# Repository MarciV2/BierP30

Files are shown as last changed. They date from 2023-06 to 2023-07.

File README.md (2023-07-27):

# BierP30 / Weißer Hase / Keba P30 Bierzapfsäule

Servus Melissi und E-Bastian,
Ich hoffe, euch hat unser Geschenk gefallen!

Damit ihr's auch öfters verwenden könnt hier eine kleine Anleitung und ein paar Tipps.

## Funktionsweise
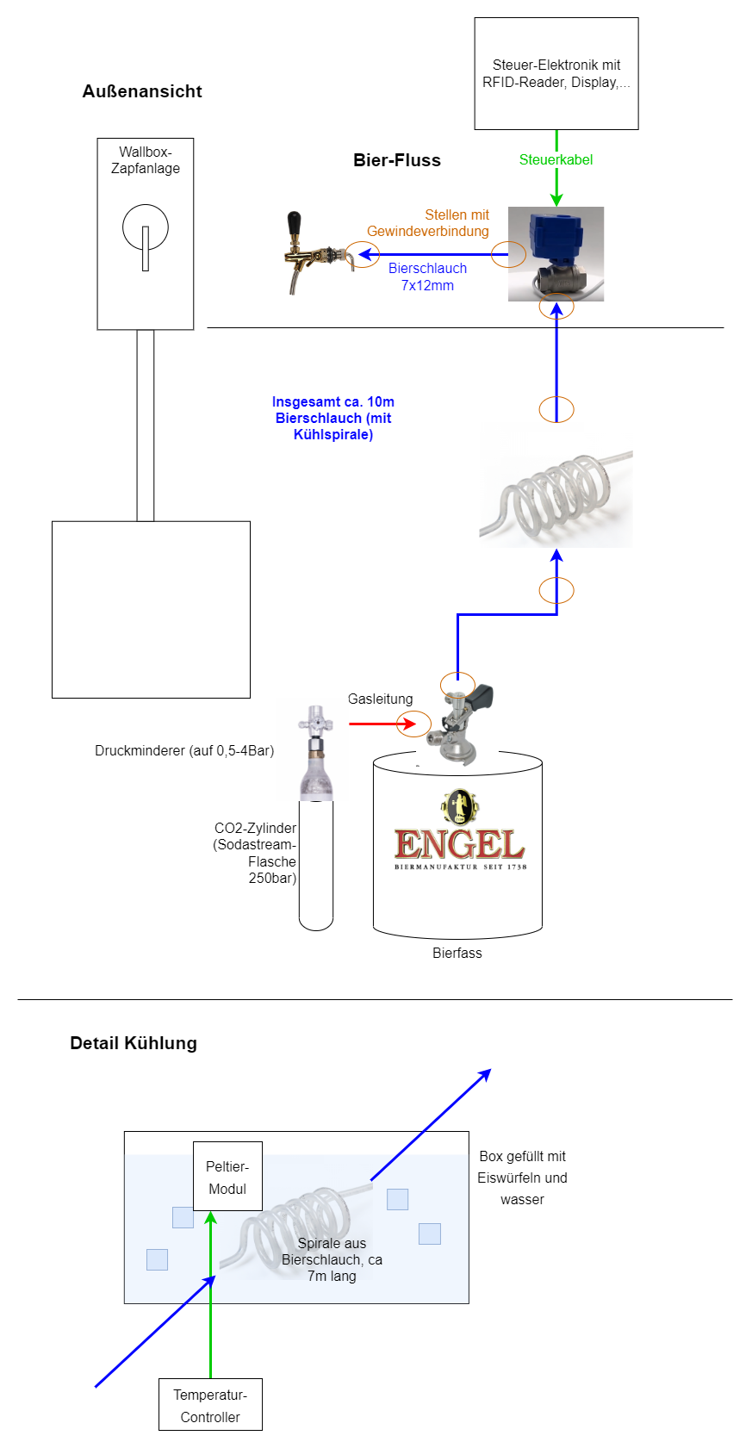
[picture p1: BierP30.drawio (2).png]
BierP30.drawio (2).png


Das Bier befindet sich anfangs im (idealerweise vorgekühlten) Fass, CO2 in der Sodastream-Flasche.
Prinzipiell wird das Gas (über einen Druckminderer) und den Fassanschluss (seitlicher Anschluss) in das Fass geleitet, wo es von oben auf das Bier drückt. Das Bier kann über ein Steigrohr im Fass durch den oberen Anschluss des Fassanschlusses und die Schläuche raus.
Das Bier fließt dann durch die Schlauchspule, welche sich in Eiswasser befindet, gekühlt in die Wallbox hoch. (den Kasten mit "Peltier-Modul" bitte ignorieren, das Feature mussten wir leider weglassen) Oben in der Wallbox ist ein Servo-getriebenes Kugelventil, das durch die Steuer-Elektronik geöffnet oder geschlossen werden kann. Beim Ausschalten der Anlage bleibt das Ventil im aktuellen Zustand. Dies ist relevant, wenn ihr nicht jedes Mal eine Karte vorhalten wollt oder zum Reinigen.
Vom Ventil fließt das Bier zum Zapfhahn. (Mehr dazu im Kapitel [Zapfen](##Zapfen))
Durch den Zapfhahn dann ins Glas und von dort dann endlich eure Rachen hinunter.

## Aufbauen
1. Bleck-Box in die Holz-Box stellen
2. etwa 6kg Eiswürfel in die Blech-Box füllen
3. (idealerweise kaltes) Wasser in die Blech-Box bis etwa 8cm unter dem Rand füllen
4. Deckel der Blech-Box mit der Kühlspirale aufsetze, sodass isolierter Schlauchabgang nahe an der Holzwand ist
5. 3-Poligen Stecker von Deckel der Blech-Box an Spelsberg-Gehäuse anschließen
6. (zuvor auf Minimum gedrehten) Druckminderer auf Sodastream-Flasche drehen (zischt mal kurz, einfach weiter drehen)
7. Sodastream-Flasche mit Spanngurt an Bierfass befestigen
8. Gasleitung von Druckminderer an seitlichen Anschluss des Fassanschlusses anschließen
9. weißes Plastikteil mit dem Keil nach oben (Rundung unten!!!) in den oberen Anschluss des Fassanschlusses legen (soll wohl helfen, dass es weniger schäumt)
10. Bierschlauch an oberen Anschluss des Fassanaschlusses anschließen und am anderen Ende an das nicht isolierte Schlauchstück der Kühlspirale. Schlauch in die vorgesehene Aussparung in Holz-Box legen. Zur Verbindung von Bierschläuchen werden die "Rohrstücke" mit den "Flügeln" verwendet.
11. Schaumstoff-Isolierung um Bleck-Box platzieren (evtl. mit Spanngurt sichern)
12. Deckel der Holz-Box (mit U-Profil und Wallbox) teilweise auf die Holz-Box setzen
13. Stecker von Wallbox an Spelsberg-Gehäuse anschließen
14. Bierschlauch von Wallbox an isolierten Abgang von Kühlspirale mittels "Rohrstück mit den Flügeln" anschließen
15. Holz-Deckel sauber auf Holz-Box aufsetzen (Deckel hat ebenfalls Aussparung für Bierschlauch)
16. Fassanschluss auf Fass schieben und Hebel nach unten drücken bis er einrastet.
17. Schuko-Stecker anschließen (wenn Kartenfunktion gewünscht oder Ventil noch geschlossen)
18. Druckminderer aufdrehen (Vollgas! (~2-2,5 Bar) Falls es pfeift -> minimal runterdrehen)

## Zapfen
1. Ladekarte vorhalten und erstmal 2-5l Schaum zapfen (da kommt am Anfang immer sehr viel!! nicht wundern)
2. Der seitliche Hebel am Zapfhahn steuert die Durchflussmenge. Idealerweise mit sehr wenig (oben) starten und beim Zapfen dann öffnen (nach vorne/unten), bis akzeptabel viel Schaum kommt.
3. Wenn der seitliche Hahn ohne übermäßigen Schaum aufgedreht werden kann, evtl den Druck am Druckminderer etwas geringer einstellen. Schaum ist eine Balance zwischen Temperatur, Druck und Durchfluss, wenn das Bier zu warm ist, schäumt es stärker, wenn der Durchfluss zu hoch ist ebenso. Bei zu wenig Schaum (wird vermutlich nicht vorkommen) könnte es zu viel Druck oder Reste vom Reinigen sein. Andere Biersorten schäumen ebenfalls sehr verschieden.
4. Für Cola, Sprudel,... ist ein deutlich höherer Druck als für Bier notwendig. Dazu bräuchtet ihr dann einen anderen Druckminderer (+ Gasflasche) aber wer will schon Sprudel, wenn man Bier haben kann?!?

Wenn bei warmem Wetter länger nichts gezapft wurde evtl. die ersten 100ml wegschütten, da diese im Schlauch zur Wallbox hoch schnell warm werden.

## Zerlegen

## Reinigen

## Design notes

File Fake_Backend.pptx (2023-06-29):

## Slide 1

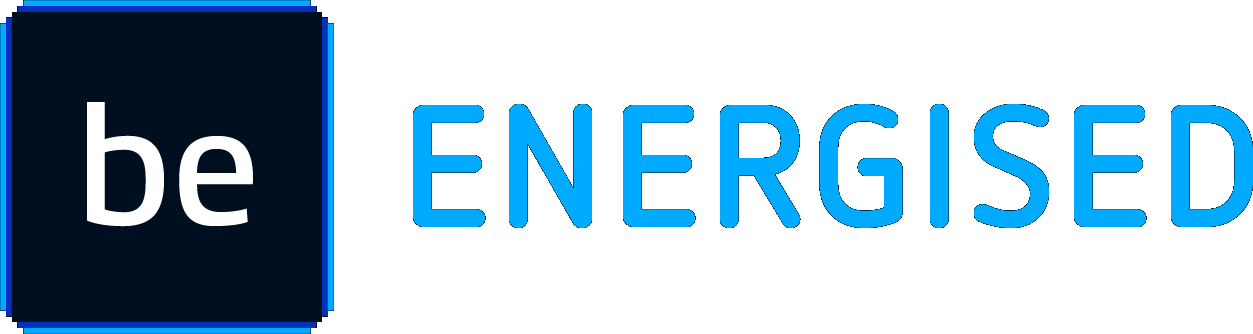
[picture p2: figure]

Dashboard

DB Hochzeit Sebastian & Melissa

Infrastruktur CRM Finanzen Aufgaben Einstellungen

>

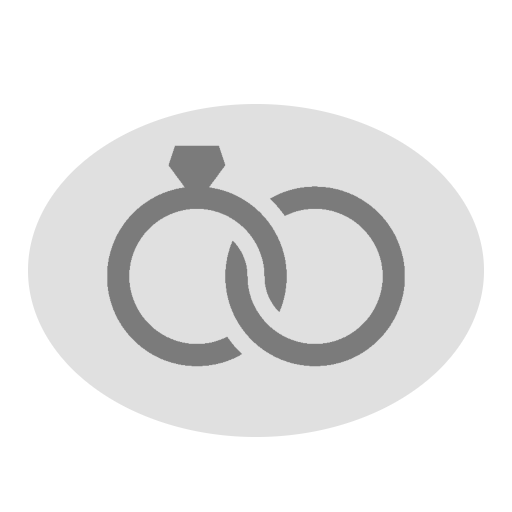
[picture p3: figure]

>

>

>

>

12

Jahre zusammen

1

Tage verheiratet

Tage verheiratet

1

Platzhalter Gruppenbild

Ganz viel Glück, Freude und Spaß wünschen euch die TSE-ler

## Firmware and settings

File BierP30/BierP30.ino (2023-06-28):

#include <SPI.h>
#include <Wire.h>


int BEER_VALVE_OPEN_TIME = 40;
#define BEER_VALVE_RELAIS_PIN 5

long beer_valve_open_millis = 0;
bool beer_active = false;

bool refill_ice = false;



void setup() {
  Serial.begin(9600);
  Serial.println("Starting...");
  SPI.begin();  // Init SPI bus
  Wire.begin(); 


  initLedMatrix();
  initLedStripe();
  initRFID();
  initTemp();

 
  pinMode(BEER_VALVE_RELAIS_PIN, OUTPUT);
  digitalWrite(BEER_VALVE_RELAIS_PIN, LOW);
}

void loop() {

  //Timer checks
  if (beer_active) {
    //Timer-Bar anpassen
    long beer_millis_elapsed = millis() - beer_valve_open_millis;
    uint8_t beer_timer_percent = 100 - round(beer_millis_elapsed / (BEER_VALVE_OPEN_TIME * 10));
    setBeerTimerBar(beer_timer_percent,255,170,0,false);

    //Zapfphase zu ende -> stoppen
    if (beer_timer_percent <= 0) {
      stopBier();
    }
  }

  displayTimerEvent();
  ledStripeTimerEvent();
  rfidTimerEvent();
  tempTimerEvent();
  
}



// Funktion wird aufgerufen, wenn Autentifizierung mit FreiBierKarte erfolgreich
void startBier() {
  beer_valve_open_millis = millis();
  digitalWrite(BEER_VALVE_RELAIS_PIN, HIGH);
  beer_active = true;
  if(refill_ice) displayMessage("Eis nachfuellen", false);
  else displayMessage("Ozapft is", false);
}


void abortBier(){
  setBeerTimerBar(100,255,0,0,true);
  digitalWrite(BEER_VALVE_RELAIS_PIN, LOW);
  beer_active = false;
}

// Funktion wird aufgerufen, wenn der Timer des Biers abgelaufen ist
void stopBier() {
  Serial.println("Timer abgelaufen, Prost!");
  digitalWrite(BEER_VALVE_RELAIS_PIN, LOW);
  beer_active = false;
  displayMessage("Prost", true);
  setBeerTimerBar(100,0,0,255,true);

}

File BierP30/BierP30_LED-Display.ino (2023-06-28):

#include <MFRC522.h>
#include <MD_Parola.h>
#include <MD_MAX72xx.h>
#include <Adafruit_NeoPixel.h>

//Matrix-Display
#define LED_MATRIX_CS 3
#define HARDWARE_TYPE MD_MAX72XX::FC16_HW
#define MAX_DEVICES 3
MD_Parola P = MD_Parola(HARDWARE_TYPE, LED_MATRIX_CS, MAX_DEVICES);
uint8_t scrollSpeed = 600;  // default frame delay value
textEffect_t scrollEffect = PA_SCROLL_LEFT;
textPosition_t scrollAlign = PA_LEFT;
uint16_t scrollPause = 1500;  // in milliseconds
char defaultMessage[] = "Karte bitte";
char curMessage[16] = { " " };  // used to hold current message

//LED-Stripe
#define LED_PIN 4
#define LED_COUNT 19
Adafruit_NeoPixel strip(LED_COUNT, LED_PIN, NEO_GRB + NEO_KHZ800);


//Zurücksetzen von Fehlermeldungen/Ende-Meldung
#define DISPLAY_DEFAULT_DELAY 5
long display_start_millis = 0;
bool display_runsOut = false;
bool ledStripe_runsOut=false;

//Led-Stripe Idle-Blinken
#define LED_STRIPE_IDLE_INTERVAL 2
long ledStripe_idleToggle_millis=0;
bool ledStripeIdle=true;
bool ledStripeCurrentlyOn=false;


void initLedMatrix(){
  // Matrix-LED-Modul initiieren
  P.begin();
  P.setSpeed(scrollSpeed);
  P.setTextAlignment(PA_LEFT);
  P.displayClear();
  P.displayReset();
  strcpy(curMessage, defaultMessage);
  P.displayText(curMessage, scrollAlign, scrollSpeed, scrollPause, scrollEffect, PA_PRINT);
}

void initLedStripe(){
  // LED-Stripe
  strip.begin();             // INITIALIZE NeoPixel strip object (REQUIRED)
  strip.show();              // Turn OFF all pixels ASAP
  strip.setBrightness(255);  // Set BRIGHTNESS to max
}

// Setzt die LED-Bar auf den angegebenen Prozentsatz (von links), mit der Farbe in RGB und resetted (wenn aktiviert) zusammen mit Display-Text
void setBeerTimerBar(uint8_t percent, uint8_t red, uint8_t green, uint8_t blue, bool runsOut) {
  ledStripeIdle=false;
  ledStripe_runsOut=runsOut;
  uint8_t ledNr = round(percent * LED_COUNT / 100.)+2;
  Serial.print("LedBar: ");
  Serial.println(ledNr);
  for (uint8_t i = 0; i <= LED_COUNT; i++) {
    if (i < ledNr) strip.setPixelColor(LED_COUNT-i, strip.Color(red, green, blue));
    else strip.setPixelColor(LED_COUNT-i, strip.Color(0, 0, 0));
  }
  strip.show();
}

//Leerlaufanimation (grünes blinken)
void doIdle(){
  if(ledStripeCurrentlyOn) setBeerTimerBar(0,0,0,0,false);
  else {
   if(refill_ice) setBeerTimerBar(100,255,0,0,false);
   else setBeerTimerBar(100,0,255,0,false);
  }
  ledStripeCurrentlyOn=!ledStripeCurrentlyOn;
  ledStripeIdle=true;
}

// Zeigt die angegebene Nachricht im Display sofort an
void displayMessage(char msg[], bool runsOut) {
  strcpy(curMessage, msg);
  P.displayClear();
  P.displayReset();
  if (runsOut) {
    display_start_millis = millis();
    display_runsOut = true;
  } else display_runsOut = false;
}


void displayTimerEvent(){
  //Display Anzeige evtl erneut starten
  if (P.displayAnimate())  // If finished displaying message
  {
    //Bei Störungsmeldung evtl zurücksetzen
    if (display_runsOut && millis() > (display_start_millis + DISPLAY_DEFAULT_DELAY * 1000)) {
      displayMessage(defaultMessage, false);
      display_runsOut = false;
      setBeerTimerBar(0,0,0,0,false);
    setLedStripeIdle();
    }
    P.displayReset();  // Reset and display it again
  }
}

//LED-Bar bei Idle-Animation toggeln (bei Auslaufender Meldung auf Idle setzen in displayTimerEvent, damit msg und stripe gleichzeitig geändert werden!)
void ledStripeTimerEvent(){
  
  //Idle-Animation
  if(ledStripeIdle && millis()>(ledStripe_idleToggle_millis+LED_STRIPE_IDLE_INTERVAL*1000)){
    doIdle();
    ledStripe_idleToggle_millis=millis();
  }
}

void setLedStripeIdle(){
  //setzen, sodass nächster timer-durchlauf die LED aktiviert und das Blinken beginnt
  ledStripeIdle=true;
  ledStripe_idleToggle_millis=millis()-(LED_STRIPE_IDLE_INTERVAL+1)*1000;
  ledStripeCurrentlyOn=false;

}
